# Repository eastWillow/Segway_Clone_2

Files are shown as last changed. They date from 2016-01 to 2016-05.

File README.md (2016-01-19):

# Segway_Clone_2
Using Three Arduinos to made the Segway. Because It is fun . :)

I am using MPU6050 to be a main sensor.
2016/1/20 Testing clock source which is the most "precision" to get the value. (Using Excel to caluuate the Standard Deviation)
2016/1/20 Setting the DLPF to reduce the Arduino performance in caluuating.
NEXT -> Change the Sensor Sensity lower to avoid the Noise ( Maybe ~)

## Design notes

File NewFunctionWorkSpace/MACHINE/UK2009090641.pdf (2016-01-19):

## projects elektorwheelie

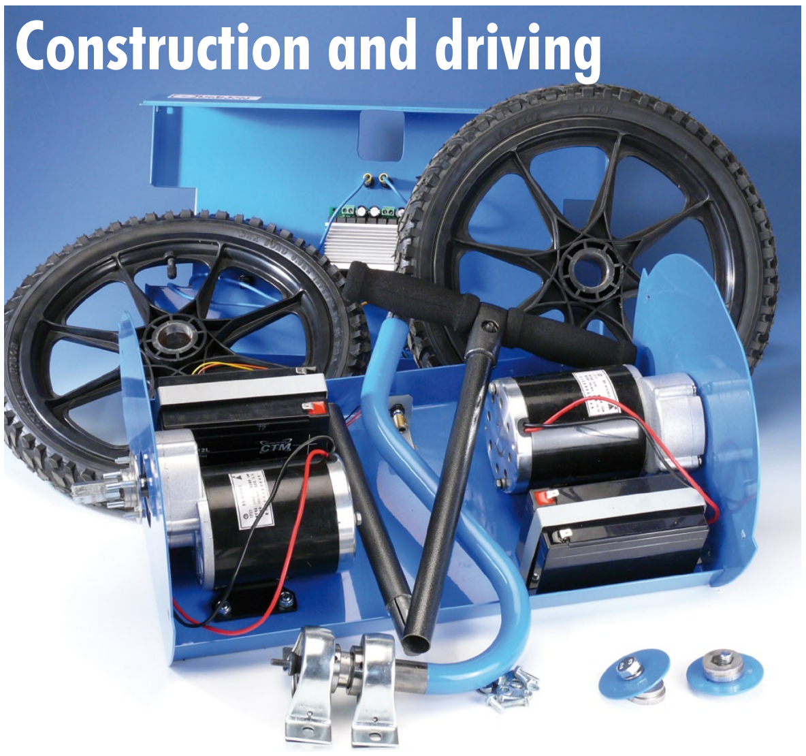
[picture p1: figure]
Construction and driving

### 64 elektor - 9/2009

The ElektorWheelie is delivered as a kit containing all the necessary parts. The kit contains all electronic bits, the batteries, the steel housing, the wheels, the motors, the control lever and an economy battery charger. The printed circuit board comes completely assembled and ready mounted in the housing, just like the motors. In this article, with the help of a few photographs, we describe what remains to be done by you.

### DIY tinkering

1. The main things you have to do yourself is mounting the control lever and attaching the wheels.
2. We start with the control lever. For this you need the brackets/bearing mounts and four bolts with matching washers and nuts.
3. The mounting brackets/bearing mounts are attached with the bolts to the middle of the base plate (between the motors). The housing already has the mounting holes for these. Tighten the bolts firmly so that they cannot come loose due to vibrations.
4. Now you need to attach the coupling between the control lever and the potentiometer. Start by adjusting the potentiometer to roughly the centre position. Make sure there is sufficient free movement clockwise as well as anti-clockwise because the pot is used to determine the position of the control lever.

# ElektorWheelie

In the first instalment about the self-balancing single-axle electric ‘vehicle’ in the Summer Circuits issue we explained the operation of the electronics. There is, of course, also some mechanical construction required before the ElektorWheelie is ready to be used.

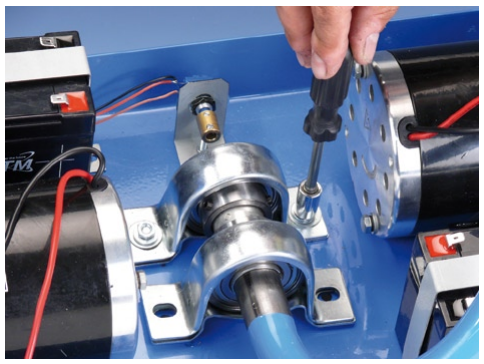
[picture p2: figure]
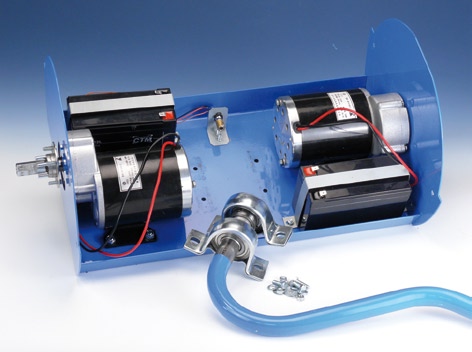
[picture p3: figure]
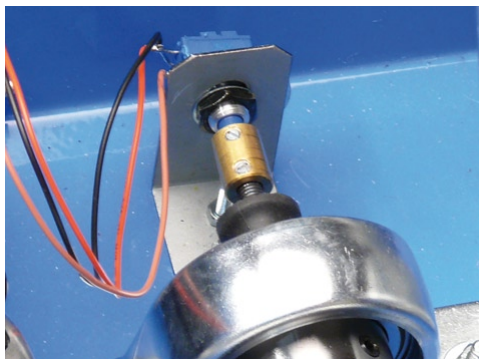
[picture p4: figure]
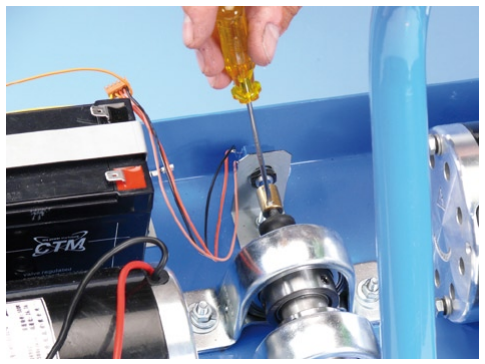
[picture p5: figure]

9/2009 - elektor | 65
5. Now turn to the cabling. The wiring diagram shows the electrical connections effectively made. Note that some cables may be a bit short for the next step and should be connected afterwards.
6. You can now slide the cover at an angle over the control lever and fasten it at the sides with four screws. After this you attach the wheels and the two remaining parts of the control lever. Make sure the large wheel nuts are fastened securely! As already mentioned, the kit is supplied with a simple charger. A complete battery charging cycle takes about 16 hours. An improved charger based on an earlier Elektor design is described elsewhere in this issue. This circuit ensures that the batteries can be charged independently so no imbalance can occur in respect of individual capacity. Before the first trip it is a good idea to test whether the ElektorWheelie functions properly. To do this, place the Wheelie on a crate or box with the wheels off the ground. Turn the Wheelie on and check whether it responds correctly to tilting forwards and backwards. Also check the operation of the control lever.

### The first trip

To allow you to drive the ElektorWheelie, you first need to insert the double pin of the Safety Switch. The electronics can now be turned on with the Main Switch. Hold the Wheelie upright, in the position in which you will drive it (base plate as horizontal as possible). The electronics will calibrate itself in this position and will attempt to maintain this position when you are driving the Wheelie.
Now place your right foot on the Foot Switch built into the base plate. This switch lets the electronics know that you have stepped onto the Wheelie. You can now test the Wheelie by leaning forwards or backwards a little and check whether the Wheelie moves with it. The foot switch is part of the safety for the Wheelie, a little more about that later.
Now put your other foot on the ElektorWheelie platform. It is important that you stand fully upright and not bend your knees! It also helps if you look straight ahead, not down. You accelerate by moving your weight towards your toes. Don’t push against the control lever, that doesn’t work well. To slow down you move your weight towards your heels. The electronics in the vehicle ensures that you will remain balanced and that you can remain standing on the balancing two-wheeler as demonstrated in the ElektorWheelie video on YouTube.
Steering is done with the control lever. Push it to the left slightly and the left motor will turn a little slower, so that the Wheelie will make a left turn. A small deflection to the right and the Wheelie will veer to the right.
When the rider is no longer standing on the base plate, the current to the motors is interrupted after a short delay (hysteresis), so that the Wheelie will not carry on and decide for itself where to go. As an additional safety feature the ElektorWheelie is fitted with an emergency stop (Safety Switch). This works as follows: A pin is attached with a cord to a strap around your arm. Should you fall unexpectedly then the pin will be pulled out by the cord, causing the motors and electronics to be switched off instantly.

### Tips

Make the first trip with the assistance of someone else! All

## projects elektorwheelie

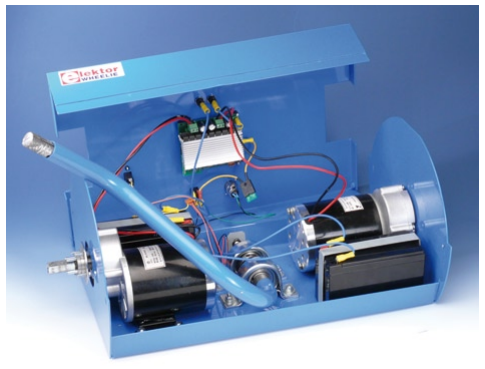
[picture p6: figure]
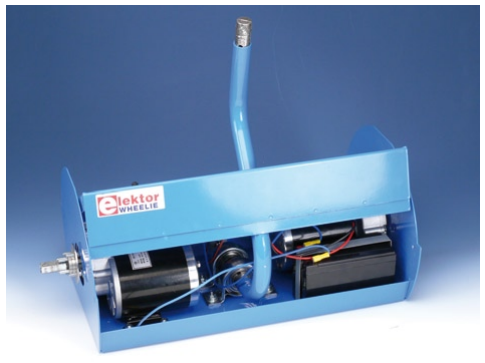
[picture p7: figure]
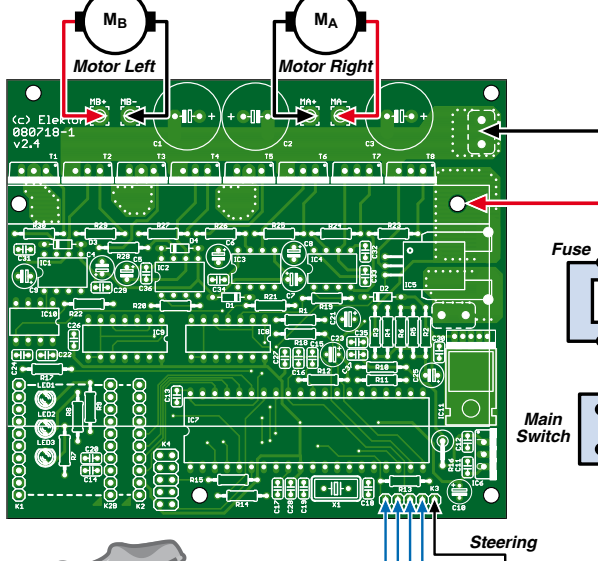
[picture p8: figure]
Steering; Main Switch; Fuse; Motor Left; Motor Right

### 66 elektor - 9/2009

sorts of things can go wrong. Helmet, knee and elbow protection are certainly recommended initially.

The software controlling the ElektorWheelie vehicle is ‘open’. That means that you can adapt and change the firmware to your heart’s content, but at your own risk. However, the supplied software has passed thorough testing and has had extensive development and is therefore very suitable without any further changes.

You are also invited to visit the ElektorWheelie forum on our website at www.elektor.com/forum. There you can discuss and gather ideas about the software and the hardware and, of course, share your experiences with other Elektor readers.

(090249-I)

2
3

1

XLR

12V

Battery

Foot Switch

090249 - 11

Safety
Switch

Battery

12V

Notice
This article provides a brief overview of the assembly of a preproduction sample. Each ElektorWheelie kit supplied to customers comes with an extensive construction manual. A pdf file of the manual will be available as a free download from www.elektor.com/ wheelie in due course. Photos, videos and impressions may be found in the ElektorWheelie blog at http://ewheelie.blogspot.com.

The wiring diagram
shows how all the parts are to be connected together.
Pay careful attention
to the polarity of the
batteries and the
connections to the motors
(do not swap left and right).

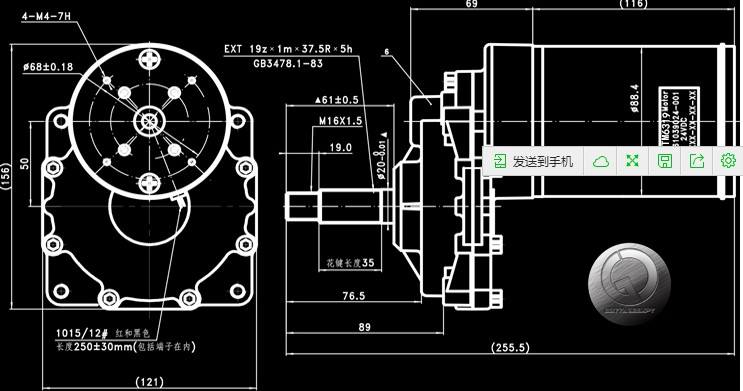
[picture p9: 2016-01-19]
NewFunctionWorkSpace/MACHINE/馬達.jpg

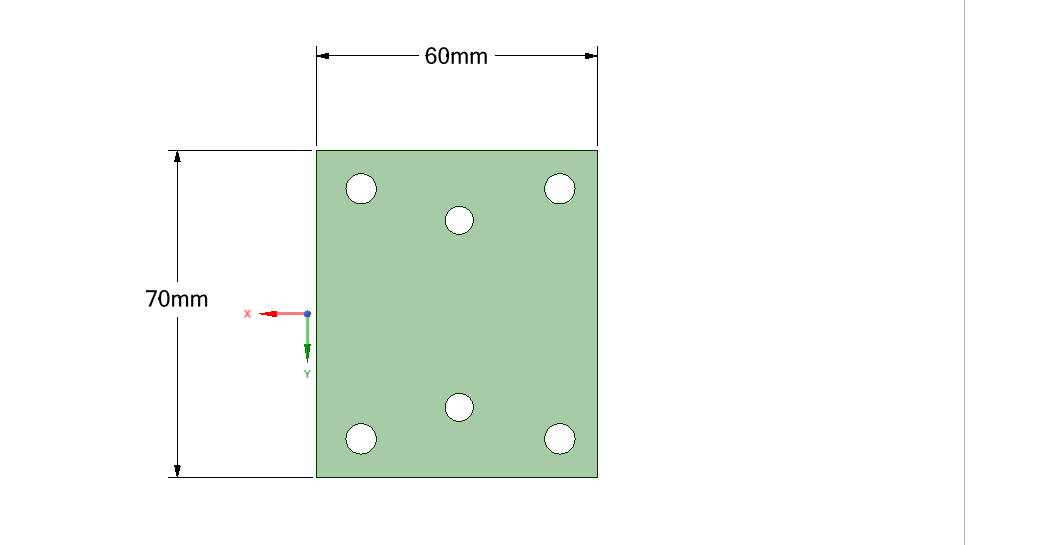
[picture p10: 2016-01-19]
NewFunctionWorkSpace/MACHINE/TurningPlate.png

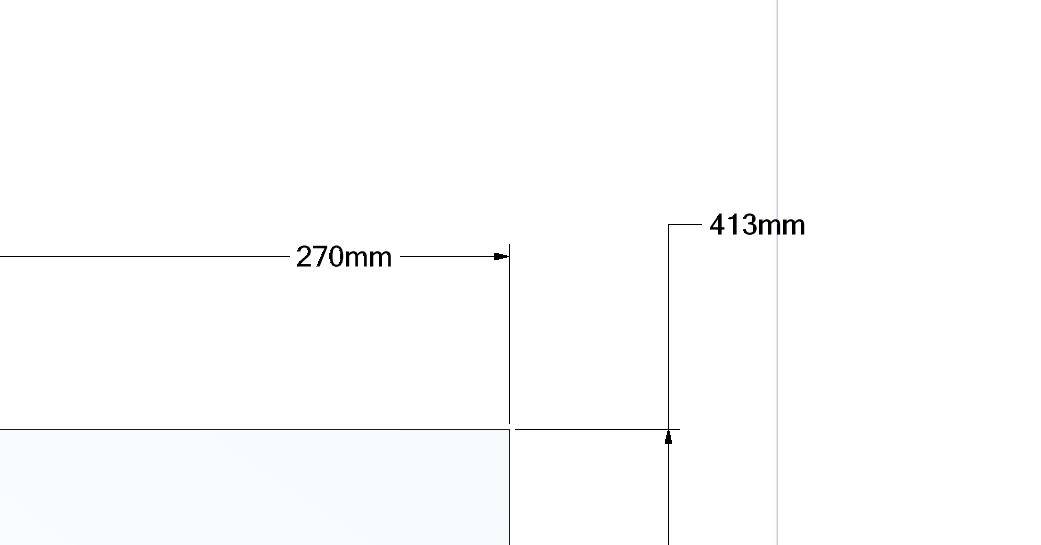
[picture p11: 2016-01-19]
NewFunctionWorkSpace/MACHINE/Top_Box_Weight5mm.png

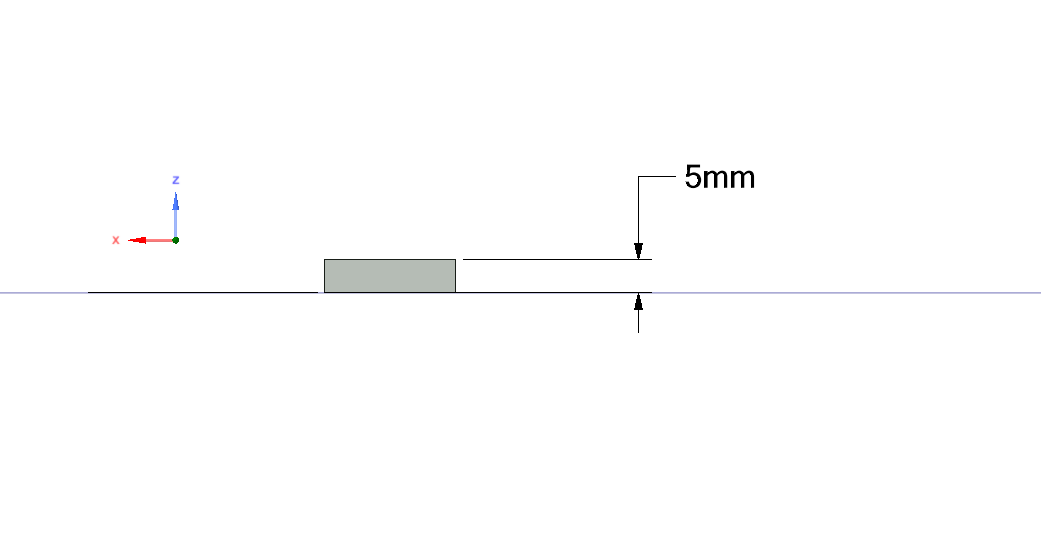
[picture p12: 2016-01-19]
NewFunctionWorkSpace/MACHINE/Controller_Left.png

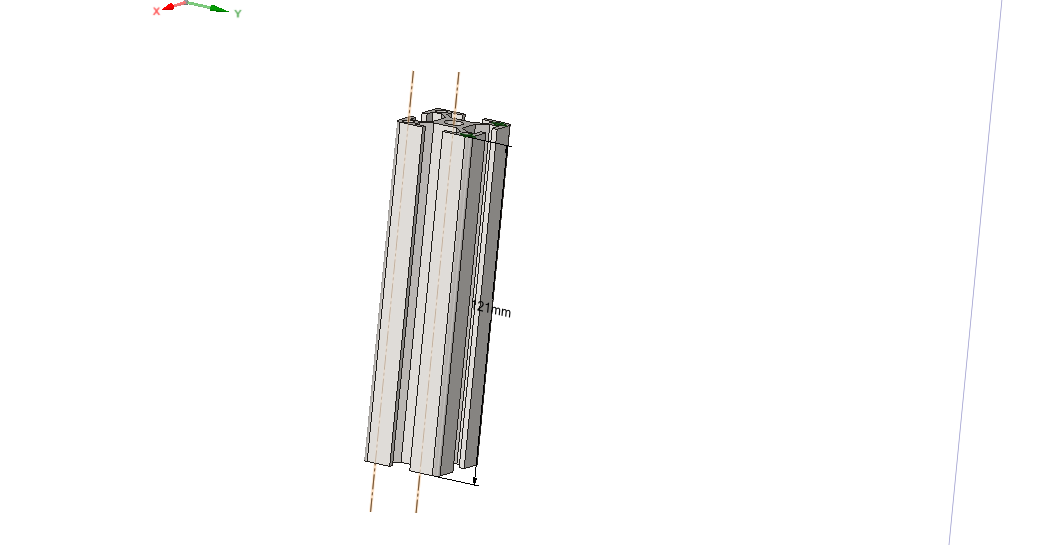
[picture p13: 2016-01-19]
NewFunctionWorkSpace/MACHINE/Aluminum extrusion 121mm_8 pices.png

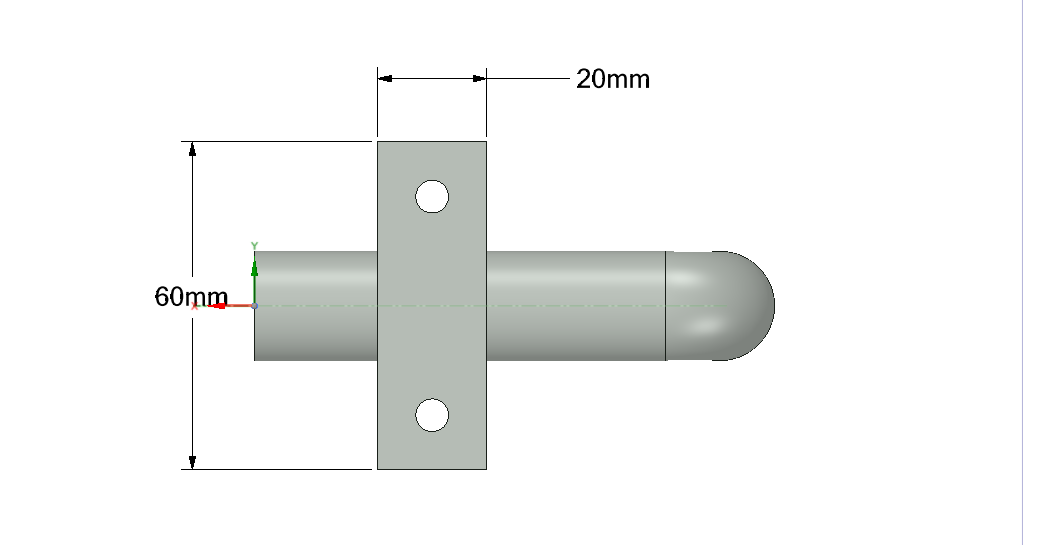
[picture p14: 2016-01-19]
NewFunctionWorkSpace/MACHINE/Controller_Bottom.png

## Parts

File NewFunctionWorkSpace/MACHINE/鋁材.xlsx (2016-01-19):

品項 | 尺寸(mm) | 數量
鋁板 | 20*60*3 | 1
鋁板 | 275*415*5 | 2
鋁板 | 60*70*3 | 1
鋁擠型 | 30*30*150 | 9
L 型角鋁 | 18.5*18.5 厚度：3mm 長度 125 | 5
如果沒有以上的尺寸，請選擇大於尺寸的規格品，謝謝

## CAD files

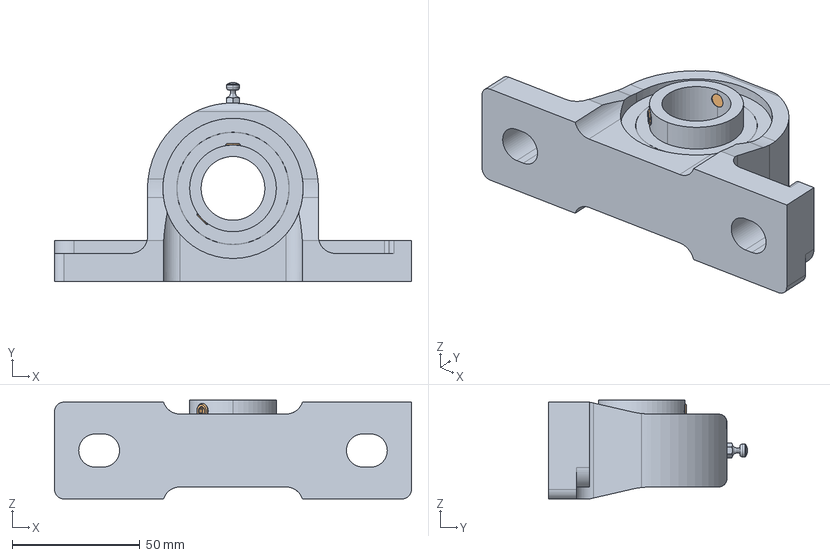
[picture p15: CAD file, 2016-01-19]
NewFunctionWorkSpace/MACHINE/PDR25.stp
140.0 x 78.0 x 38.8 mm

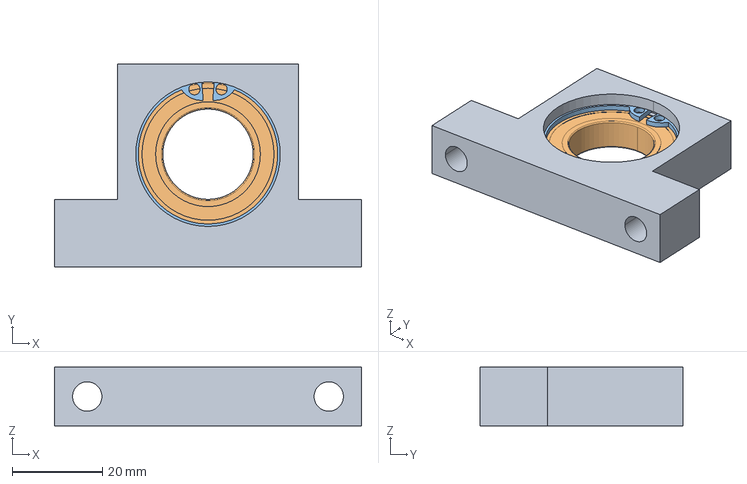
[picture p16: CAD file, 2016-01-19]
NewFunctionWorkSpace/MACHINE/BGHFB6804ZZ-25.stp
68.0 x 45.0 x 13.0 mm

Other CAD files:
NewFunctionWorkSpace/MACHINE/Motor_Wheel_Test.CATProduct
NewFunctionWorkSpace/MACHINE/Part1.CATPart
NewFunctionWorkSpace/MACHINE/Part2.CATPart
NewFunctionWorkSpace/MACHINE/Part3.CATPart

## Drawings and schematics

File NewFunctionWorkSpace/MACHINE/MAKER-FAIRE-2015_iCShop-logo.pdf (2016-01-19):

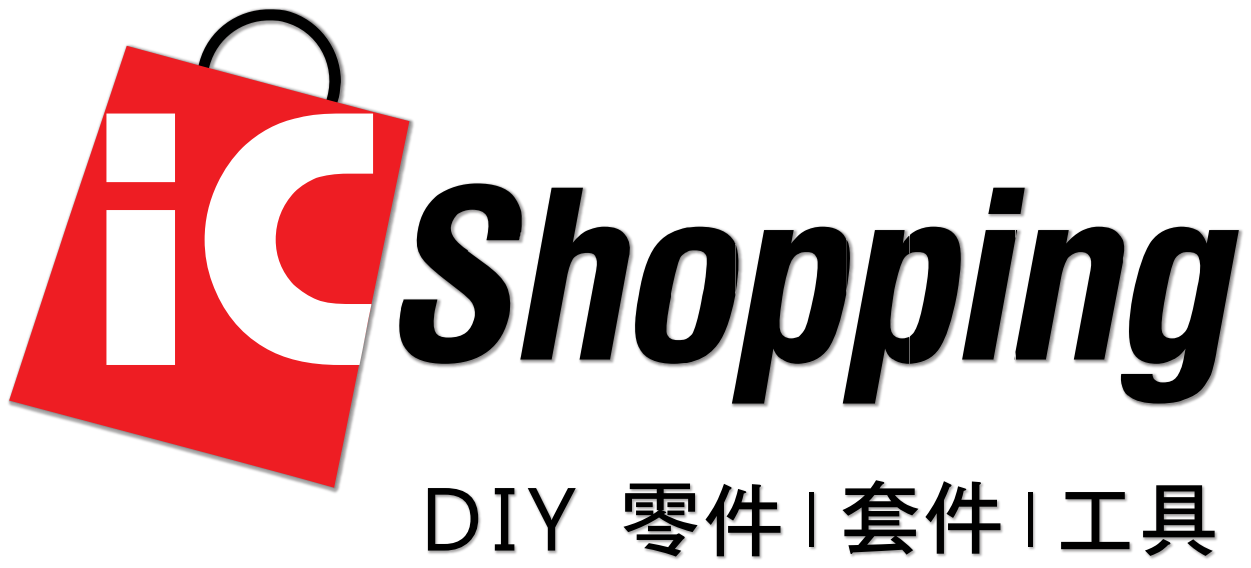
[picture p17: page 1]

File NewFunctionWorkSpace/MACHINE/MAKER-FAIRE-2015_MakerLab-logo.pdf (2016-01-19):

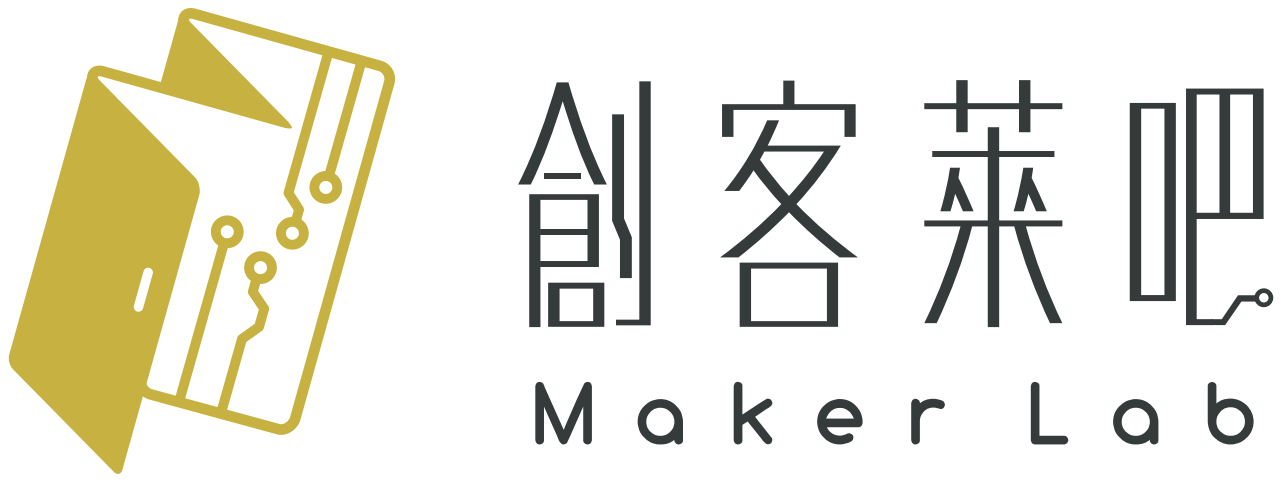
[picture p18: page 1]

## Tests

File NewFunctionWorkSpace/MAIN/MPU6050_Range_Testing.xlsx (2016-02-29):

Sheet: Range(0)
2473 | 16364 | -48 | 30 | 3 | -13 | -8 | avg | 16378.69341 | -61.32399697 | 31.45420136 | 1.342922029 | 1.720666162 | 1.55336866
2477 | 16350 | -58 | 24 | 2 | -9 | -8 | ds | 12.47570941 | 12.50823587 | 18.79650134 | 2.422556179 | 5.571361141 | 4.882300334
2480 | 16346 | -70 | 42 | -2 | -4 | -6
2483 | 16350 | -66 | 60 | -2 | -4 | -5
2486 | 16344 | -62 | 64 | -4 | -3 | -4
2489 | 16348 | -64 | 78 | -4 | -4 | -4
2491 | 16346 | -68 | 88 | -3 | -4 | -3
2494 | 16354 | -66 | 74 | -5 | -3 | -1
2497 | 16352 | -66 | 76 | -3 | -2 | 1
2500 | 16362 | -62 | 60 | 0 | -3 | 0
2503 | 16350 | -60 | 50 | -2 | -4 | -2
2505 | 16356 | -58 | 50 | -1 | -2 | -3
2508 | 16362 | -66 | 74 | 1 | -3 | -1
2511 | 16348 | -56 | 74 | -3 | -5 | -4
2514 | 16356 | -50 | 68 | 0 | -6 | -4
2518 | 16380 | -56 | 62 | 1 | -6 | -2
2520 | 16382 | -52 | 48 | -1 | -5 | -3
2523 | 16384 | -54 | 48 | 2 | -2 | -2
2526 | 16392 | -50 | 46 | 2 | 0 | -2
2529 | 16394 | -54 | 40 | 4 | -2 | 1
2532 | 16392 | -62 | 38 | 4 | 1 | 1
2534 | 16376 | -60 | 36 | 5 | 1 | 2
2537 | 16376 | -54 | 58 | 3 | 4 | 3
2540 | 16356 | -50 | 50 | 3 | 2 | 4
2543 | 16358 | -52 | 46 | 3 | 2 | -1
2545 | 16354 | -56 | 40 | 3 | 4 | -1
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

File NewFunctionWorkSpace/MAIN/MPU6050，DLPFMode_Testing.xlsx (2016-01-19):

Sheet: setDLPFMode(0)
2244 | 16356 | 316 | -280 | -6 | 7 | -16 | 2241.680553 | 249.5027369 | 124.4136988 | 135.3953782 | 21.52174175 | 41.4550447
2246 | 16452 | 380 | -212 | 22 | -4 | -8
2249 | 16380 | 304 | -132 | -19 | 17 | 17
2252 | 16396 | 356 | -204 | 19 | -9 | 19
2255 | 16520 | 256 | -232 | 6 | 32 | 39
2258 | 16240 | 304 | -212 | 11 | 28 | 20
2262 | 16304 | 356 | -128 | -21 | 34 | 24
2265 | 16356 | 272 | -204 | 11 | 24 | 13
2268 | 16400 | 320 | -304 | 23 | 29 | 23
2271 | 16360 | 152 | -136 | 10 | 5 | 3
2274 | 16404 | 232 | -192 | 0 | -3 | -8
2277 | 16248 | 284 | -208 | 8 | -24 | 5
2280 | 16452 | 256 | -180 | 15 | 20 | -25
2283 | 16308 | 272 | -212 | 6 | -39 | 6
2286 | 16524 | 140 | -276 | -1 | 16 | -12
2289 | 16220 | 312 | -196 | 0 | -9 | 3
2291 | 16380 | 216 | -244 | 24 | 8 | 9
2294 | 16404 | 268 | -68 | -17 | 9 | -15
2297 | 16284 | 320 | -152 | 19 | -13 | 2
2300 | 16480 | 192 | -84 | -13 | 4 | -15
2304 | 16324 | 372 | -180 | 0 | 14 | 6
2307 | 16500 | 200 | -160 | -4 | -21 | -9
2310 | 16380 | 320 | -372 | 7 | 27 | 22
2313 | 16396 | 224 | -120 | 21 | 6 | 8
2316 | 16432 | 316 | -256 | -6 | 25 | 30
2319 | 16272 | 168 | -112 | 20 | 17 | 23
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

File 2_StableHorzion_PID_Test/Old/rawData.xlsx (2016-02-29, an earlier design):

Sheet: Pluse_10_New
0.052 | 0 | 120.82
0.056 | 0 | 120.81
0.06 | 0 | 120.8
0.064 | 0 | 120.79
0.068 | 0 | 120.79
0.072 | 0 | 120.78
0.077 | 0 | 120.77
0.081 | 0 | 120.77
0.085 | 0 | 120.76
0.089 | 0 | 120.75
0.092 | 0 | 120.74
0.096 | 0 | 120.74
0.1 | 0 | 120.73
0.104 | 0 | 120.72
0.108 | 0 | 120.71
0.112 | 0 | 120.71
0.116 | 0 | 120.7
0.121 | 0 | 120.7
0.125 | 0 | 120.69
0.129 | 0 | 120.69
0.133 | 0 | 120.68
0.137 | 0 | 120.68
0.141 | 0 | 120.67
0.145 | 0 | 120.67
0.149 | 0 | 120.66
0.152 | 0 | 120.66
0.156 | 0 | 120.65
0.161 | 0 | 120.65
0.165 | 0 | 120.64
0.169 | 0 | 120.64
0.173 | 0 | 120.63
0.177 | 0 | 120.63
0.181 | 0 | 120.62
0.185 | 0 | 120.62
0.189 | 0 | 120.61
0.193 | 0 | 120.61
0.197 | 0 | 120.61
0.201 | 0 | 120.6
0.206 | 0 | 120.6
0.21 | 0 | 120.6
0.214 | 0 | 120.59
0.217 | 0 | 120.59
0.221 | 0 | 120.59
0.225 | 0 | 120.58
0.229 | 0 | 120.58
0.233 | 0 | 120.57
0.237 | 0 | 120.57
0.241 | 0 | 120.57
0.246 | 0 | 120.56
0.25 | 0 | 120.56
0.254 | 0 | 120.56
0.258 | 0 | 120.55
0.262 | 0 | 120.55
0.266 | 0 | 120.55
0.27 | 0 | 120.54
0.274 | 0 | 120.54
0.278 | 0 | 120.54
0.282 | 0 | 120.53
0.285 | 0 | 120.53
0.29 | 0 | 120.52
0.294 | 0 | 120.52
0.298 | 0 | 120.52
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

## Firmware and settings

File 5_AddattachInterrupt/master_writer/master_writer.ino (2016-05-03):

#include <Wire.h>
#define _S_Curve //_MANUAL_PWM, _AUTO_DEGREE, _MANUAL_SPEED _S_Curve
void setup()
{
  Wire.begin(); // join i2c bus (address optional for master)
  Serial.begin(115200);
  Serial.setTimeout(50);
  pinMode(13, OUTPUT);
  digitalWrite(13, LOW);
  interrupt_initial();
  main_set();
  ScurveInitial();
  motorCommand(2048);//Shutdown
  motorCommand(0);//Initial
  motorCommand(2048);//Shutdown
}

volatile double initialAngle = 0;
volatile double initialMillis = 0;
volatile int command = 2048;
volatile double errMillis = 0;
volatile double errAngle = 0;
volatile bool interruptResetFlag = false;
void loop()
{
#ifdef _AUTO_DEGREE
#else _S_Curve
  static double PID_target = 0;
#endif
  while (Serial.available() > 0) {
    command = Serial.parseInt();
#ifdef _MANUAL_SPEED
    if (command > 200) {
      if (command != 2048)
        command = 200;
    }
    if (command < -200) {
      command = -200;
    }
#endif
#ifdef _MANUAL_PWM
    if (command > 1023) {
      if (command != 2048)
        command = 1023;
    }
    if (command < -1023) {
      command = -1023;
    }
#endif
#ifdef _AUTO_DEGREE
    if (command > 90) {
      if (command != 2048)
        command = 90;
    }
    if (command < -90) {
      command = -90;
    }
#endif
#ifdef _S_Curve
    if (command > 200) {
      if (command != 2048)
        command = 200;
    }
    if (command < -200) {
      command = -200;
    }
#endif
  }
  sample_angle(micros());
#ifdef _MANUAL_SPEED
  motorCommand(command);
#endif
  if (command == 2048 || interruptResetFlag == true) {
    motorCommand(2048);
    interruptResetFlag = false;
    initialMillis = millis();
    initialAngle = use_CompAngle(micros());
    PIDreset();
    ScurveReset();
    digitalWrite(13, LOW);
  }
  else {
    errMillis = (millis() - initialMillis) / 1000.0;
    errAngle = initialAngle - use_CompAngle(micros());
    Serial.print((double)errMillis, 4);
    Serial.print('\t');
    Serial.print(command);
    Serial.print('\t');
#ifdef _AUTO_DEGREE
    PID_target = PID(errAngle, command);
    motorCommand(PID_target);
    Serial.print(PID_target);
    Serial.print('\t');
#endif
#ifdef _S_Curve
    PID_target = PID(errAngle, command);
    ScurveCommand(PID_target, errMillis);
    motorCommand(ScurveSpeedOutput());
    Serial.print(PID_target);
    Serial.print('\t');
#endif
    Serial.println(errAngle);
  }
  digitalWrite(13, HIGH);
}

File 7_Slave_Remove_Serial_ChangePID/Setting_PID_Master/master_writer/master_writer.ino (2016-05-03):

#include <Wire.h>
#define motorOff true
#define motorOn false
#define motorHeart random(128)
void setup()
{
  Wire.begin(); // join i2c bus (address optional for master)
  Serial.begin(115200);
  Serial.setTimeout(20);
  pinMode(13, OUTPUT);
  interrupt_initial();
  main_set();
  ScurveInitial();
  motorCommand(0, motorOff, motorHeart);
  digitalWrite(13, HIGH);
}

volatile double initialAngle = 0;
volatile double initialMillis = 0;
volatile double errMillis = 0;
volatile double errAngle = 0;
volatile bool interruptResetFlag = false;

void loop()
{
  static double PID_target = 0;
  static int command = 0;
  while (Serial.available() > 0) {
    command = Serial.parseInt();
    if (command > 100) {
        command = 100;
    }
    if (command < -100) {
      command = -100;
    }
  }
  motorCommand(command, motorOn, motorHeart);
  if(interruptResetFlag == true){
    motorCommand(0, motorOff, motorHeart);
    interruptResetFlag = false;
    command = 0;
  }
  Serial.println(command);
}

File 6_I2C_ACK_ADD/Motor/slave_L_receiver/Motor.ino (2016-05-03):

#define ENCODER_USE_INTERRUPTS
#define _LEFT
#define _NODEBUG
/*
本次只有傳送pluse 給 Matlab 剩下運算在電腦端
*/
#include <Encoder.h>
#include <TimerOne.h>
#include <TimerThree.h>

#define PWM1 9
#define PWM2 11
#define EN 8
#define CYCLE_PLUSE 17408.0
#define CYCLE_DEGREE 360.0
#define PluseToCycle(pluse) (pluse/CYCLE_PLUSE)
#define PluseToDegree(pluse) (pluse/CYCLE_PLUSE)*CYCLE_DEGREE
#define MinPWM 200 //MAX 1023
#define motorOff true
#define motorOn false

Encoder Enc(0, 1);

volatile static long oldPosition  = -999;
volatile static long newPosition  = 0;

volatile long pluse;
volatile long last_pluse;

struct _data {
  volatile int target;
  volatile bool reset;
  volatile int heart;
} data;

static long err = 0;
static long totalErr = 0;
static unsigned int HeartCounter = 0;

void motorInitial() {
  pinMode(PWM1, OUTPUT);
  pinMode(EN, OUTPUT);
  pinMode(PWM2, OUTPUT);
  digitalWrite(PWM1, LOW);
  digitalWrite(PWM2, LOW);
  digitalWrite(EN, LOW);
  Timer1.initialize(250);  // 0.25 ms 5khz
  Timer3.initialize(10000); // 10ms = 0.01 s

  Timer1.attachInterrupt(getEncoder);
  Timer3.attachInterrupt(getRpm);

  data.target = 0;
  data.reset = motorOff;
  data.heart = random(128);
#ifdef _DEBUG
  Serial.begin(115200);
#endif
}

void Motor() {
  static long initialMillis = 0;
  static long errMillis = 0;
  static int target = 0;
  static int power = 0;

  while (data.reset == motorOff) {
    initialMillis = millis();
    err = 0;
    totalErr = 0;
    oldPosition  = -999;
    newPosition  = 0;
    power = 0;
    target = 0;
    pluse = 0;
    last_pluse = 0;
  }
  errMillis = millis() - initialMillis;
  target = data.target;
  power = PID(pluse, target);

  static int oldHeart = 0;
  if (data.heart == oldHeart) {
    HeartCounter ++;
  }
  else {
    oldHeart = data.heart;
    HeartCounter = 0;
  }
#ifndef _DEBUG
  while (HeartCounter > 190) {
#endif
#ifdef _DEBUG
    while (HeartCounter > 10) {
#endif
      while (true) {
        Timer1.pwm(PWM1, 0);
        Timer1.pwm(PWM2, 0);
        digitalWrite(13, HIGH);
        delay(500);
        digitalWrite(13, LOW);
        delay(500);
      }
    }

    if (power > 0) {
#ifdef _LEFT
      Timer1.pwm(PWM1, abs(power));
      Timer1.pwm(PWM2, 0);
#endif
#ifdef _RIGHT
      Timer1.pwm(PWM1, 0);
      Timer1.pwm(PWM2, abs(power));
#endif
    }
    else {
#ifdef _LEFT
      Timer1.pwm(PWM1, 0);
      Timer1.pwm(PWM2, abs(power));
#endif
#ifdef _RIGHT
      Timer1.pwm(PWM1, abs(power));
      Timer1.pwm(PWM2, 0);
#endif
    }
#ifdef _DEBUG
    Serial.print((double)errMillis / 1000.0, 4);
    Serial.print('\t');
    Serial.print(pluse);
    Serial.print('\t');
    Serial.print(target);
    Serial.print('\t');
    Serial.print(power);
    Serial.print('\t');
    Serial.print(HeartCounter);
    Serial.print('\t');
    Serial.println(data.heart);
#endif

  }
  void getRpm() {
    Timer3.detachInterrupt();
#ifdef _LEFT
    pluse = (newPosition) - (oldPosition);//Right Side Need to Add a Negative
#endif
#ifdef _RIGHT
    pluse = -((newPosition) - (oldPosition));
#endif
    if (abs(pluse - last_pluse) > 100) {
      pluse = last_pluse;
    }
    oldPosition = newPosition;
    last_pluse = pluse;
    Timer3.attachInterrupt(getRpm);
  }
  void getEncoder() {
    Timer1.detachInterrupt();
    newPosition = Enc.read();
    Timer1.attachInterrupt(getEncoder);
  }
  void getI2C_Data(int x) {
    void *p = &data;
    size_t dataSize = sizeof(data);
    while (Wire.available()) // loop through all but the last
    {
      for (int i = 0; i < dataSize; i++) {
        *((uint8_t*)p + i) = Wire.read();
      }
    }
  }

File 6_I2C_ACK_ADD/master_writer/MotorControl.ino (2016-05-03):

struct _data {
  int command;
  bool reset;
  int heart;
} data;

void motorCommand(int command,bool reset,int heart)
{
  void *p = &data;
  size_t dataSize = sizeof(data);
  data.command = command;
  data.reset = reset;
  data.heart = heart;
  Wire.beginTransmission('L'); // transmit to device 
  for (int i = 0; i < dataSize; i++) {
    Wire.write(*((uint8_t*)p + i));
  }
  Wire.endTransmission();    // stop transmitting
  Wire.beginTransmission('R'); // transmit to device #4
  for (int i = 0; i < dataSize; i++) {
    Wire.write(*((uint8_t*)p + i));
  }
  Wire.endTransmission();    // stop transmitting
}

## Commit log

2016-01-19 Revert "initial Commit"
    This reverts commit bcd1de7b37916d7d24303ed64a46606e85e43669.
    [20150222_2.xlsx, 20150522_1.xlsx, 20150522_NoTriger.xlsx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]
2016-01-19 Updata the next goal
    Setting the DLPF to reduce the Arduino performance in caluuating
2016-01-19 Chosing DLPFMode Done
    I chosing the 10Hz
    [MPU6050，DLPFMode_Testing.xlsx]
2016-02-29 Add S-Curve Profile in Integrator_Test
    Only Serial Output
    [20150222_2.xlsx, 20150522_1.xlsx, 20150522_NoTriger.xlsx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]
2016-03-03 Can Ride
    But Need to Tweak P gain value and Scurve Jerk Value
    [Output_Test.xlsx]
2016-03-23 Add Interrupt Reset
    [Output_Test.xlsx]
2016-05-03 Big Change
    [Output_Test.xlsx]
